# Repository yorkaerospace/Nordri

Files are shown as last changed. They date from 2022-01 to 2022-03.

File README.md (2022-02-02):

# Nordri

Nordri is a generic high-power rocket design.

## Features

- 54mm body, designed for postal tubes
- Fin assembly can be laser-cut from plywood
- Long 29mm inner tube for motor housing, designed to accommodate G and H motors up to 6 grains
- Mid-body break

## License

The designs in this repo are licensed under the [Creative Commons BY-SA 4.0 license](https://creativecommons.org/licenses/by-sa/4.0/).

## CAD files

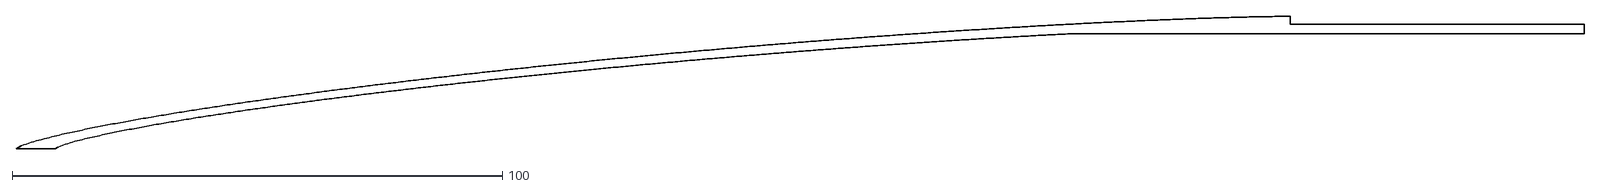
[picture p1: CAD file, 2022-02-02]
CAD/NoseSlice.dxf
320.0 x 27.0

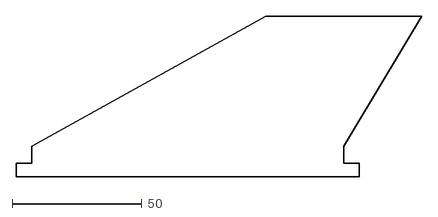
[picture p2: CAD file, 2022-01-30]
CAD/1Fin.dxf
156.0 x 61.6

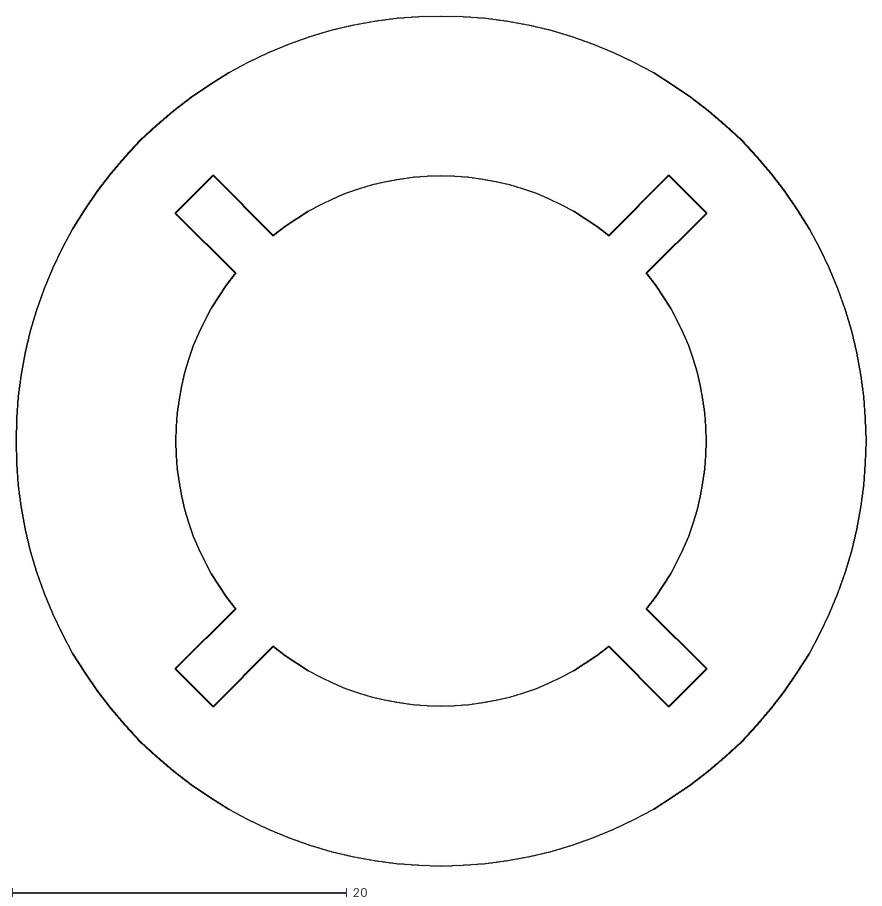
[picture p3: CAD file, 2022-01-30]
CAD/1Ring.dxf
50.8 x 50.8

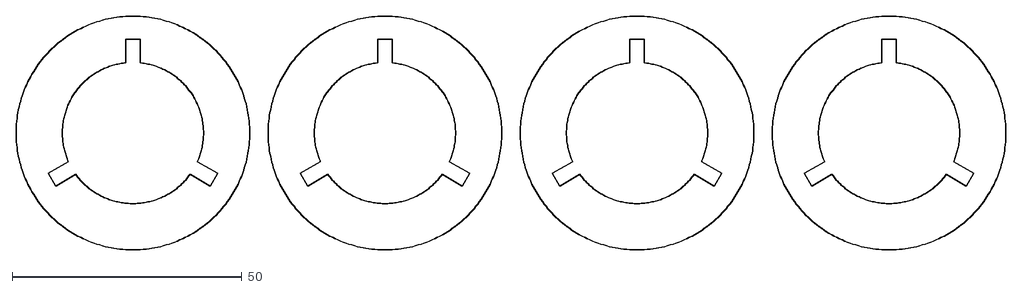
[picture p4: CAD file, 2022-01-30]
CAD/4Rings.dxf
215.2 x 50.8

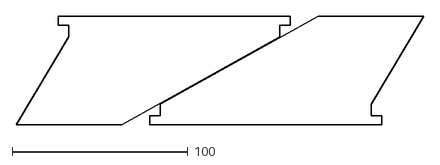
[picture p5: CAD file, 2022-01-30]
CAD/2Fins.dxf
232.0 x 61.7

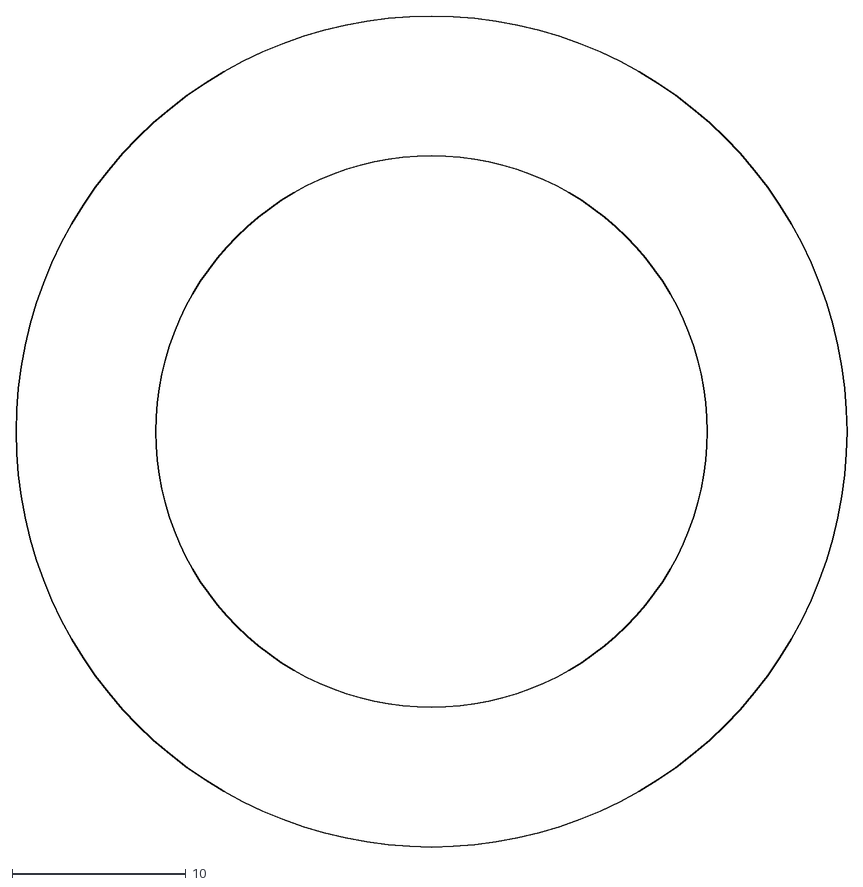
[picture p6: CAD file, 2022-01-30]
CAD/TopRing.dxf
47.8 x 47.8

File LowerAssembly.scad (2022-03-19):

// Laser Material Thickness
MATERIAL = 3.5;

// Tube dimensions
MAIN_OUTER = 54;
MAIN_INNER = 51;
COUPLER_INNER = 48.5;
TUBE_OUTER = 32;
TUBE_INNER = 29.5;
TUBE_LENGTH=200;

// Fin dimensions
FIN_THICKNESS = MATERIAL;
FIN_POINTS = [
    [0,0], [60,45], [100,45], [120,0]
];
FIN_ROOT = FIN_POINTS[len(FIN_POINTS)-1][0];
SLOT_HEIGHT = 5; // radial height of fin tabs

// Other
RING_THICKNESS = MATERIAL;
NUM_FINS = 4;
CORD_HOLE = 4; // diameter of the hole for the paracord
$fn = 100;

// Creates a 3d single fin on the xy plane aligned to 0,0
module Fin(){
    tab_len = (MAIN_OUTER - TUBE_OUTER)/2;
    linear_extrude(FIN_THICKNESS, center=true){
        union(){
            // Fin itself
            translate([0,tab_len,0]){
                polygon(FIN_POINTS);
            }
            // Main tab
            square([FIN_ROOT, tab_len], center=false);
            // Centering Slot
            translate([-RING_THICKNESS*2,-0.1,0]){
                square([FIN_ROOT + RING_THICKNESS*5, SLOT_HEIGHT+0.1], center=false);
            }
        }
    }
}

// Creates the n-fin assembly aligned around the inner tube
module Fins(){
    translate([0,0,FIN_ROOT+RING_THICKNESS*2])
    rotate([0,90,0]){
        for(i = [0 : 360/NUM_FINS : 360]){
            rotate([i, 0,0]){
                translate([0,TUBE_OUTER/2,0]){ Fin(); }
            }
        }
    }
}

// Model of the inner tube
module InnerTube(h=TUBE_LENGTH) {
    difference(){
        cylinder(h=h, d=TUBE_OUTER);
        cylinder(h=h, d=TUBE_INNER);
    }
}

module M3_nut(h=2.4, center=true) {
    // div by cos(30) converts hexagon side distance to corner distance

    LASER_TOLERANCE = 0.2;
    // Maximum width across flats (5.5)
    cylinder(h=h, d=5.5/cos(30)-LASER_TOLERANCE, $fn=6, center=center); 
    // Minimum width across flats (5.32)
    *cylinder(h=h, d=5.32/cos(30)-LASER_TOLERANCE, $fn=6, center=center); 
    // Minimum width across corners (6.01)
    *cylinder(h=h, d=6.01-LASER_TOLERANCE, $fn=6, center=center); 
}

module NutRetainer(w=10, h=3.5, nut=true){
    difference(){
        union(){
            color("red") 
            cube([w, MATERIAL*2 + h, MATERIAL], center=true);
            cube([w+8,h, MATERIAL], center=true);
        }
        if(nut) rotate(30) M3_nut(h=100);
    }
}

module Retainers(nut=false, h=3.5){
    rotate([0,90,0]){
        for(i = [360/NUM_FINS/2 : 360/NUM_FINS : 360]){
            rotate([i, 0,0]){
                translate([h/2,TUBE_OUTER/2 +4, 0]){ 
                    rotate([90,90,0]) NutRetainer(nut=nut, h=h);
                    }
            }
        }
    }
}

// Creates a ring on the xy plane with the fin slots cut out
module CouplerRing(){
    difference(){
        linear_extrude(RING_THICKNESS, center=false){
            difference(){
                circle(d=COUPLER_INNER);
                circle(d=TUBE_OUTER);
                translate([(TUBE_OUTER + CORD_HOLE) /2 -1,0,0]) circle(d=CORD_HOLE);
            }
        }
        Retainers(h=MATERIAL);
    }
}

module UpperFinRing(){
    difference(){
        linear_extrude(RING_THICKNESS, center=false){
            difference(){
                circle(d=MAIN_INNER);
                circle(d=TUBE_OUTER);
            }
        }
        Fins();
    }
}

module LowerFinRingTop(){
    difference(){
        linear_extrude(RING_THICKNESS, center=false){
            difference(){
                circle(d=MAIN_INNER);
                circle(d=TUBE_OUTER);
            }
        }
        Fins();
        for (r = [45: 180: 360]){
            rotate([0,0,r])
            translate([20,0,0])
            rotate([0,0,30]) M3_nut(h=10);
        }
    }
}

module LowerFinRingBottom(){
    difference(){
        linear_extrude(RING_THICKNESS, center=false){
            difference(){
                circle(d=MAIN_INNER);
                circle(d=TUBE_OUTER);
            }
        }
        Fins();
        for (r = [45: 180: 360]){
            rotate([0,0,r])
            translate([21,0,0])
            rotate([0,0,30]) cylinder(10,3, center=true);
        }
    }
}

// ---=== Render a pretty model ===---
module full_model(){
    InnerTube();
    // Fins in red
    color("red"){
        Fins();
    }
    translate([0,0,TUBE_LENGTH-RING_THICKNESS]) CouplerRing();
    translate([0,0,TUBE_LENGTH-RING_THICKNESS]) Retainers(nut=true);
    translate([0,0,TUBE_LENGTH-RING_THICKNESS*3]) CouplerRing();
    
    translate([0,0,FIN_ROOT + RING_THICKNESS*3]) UpperFinRing();
    translate([0,0,FIN_ROOT + RING_THICKNESS*2]) UpperFinRing();
    
    translate([0,0,RING_THICKNESS]) LowerFinRingBottom();
    translate([0,0,]) LowerFinRingTop();
    translate([0,0,-RING_THICKNESS]) LowerFinRingBottom();
}

full_model();

// Parts to cut
*projection() CouplerRing(); // x2
*projection() UpperFinRing(); // x2
*projection() LowerFinRingTop(); // x1
*projection() LowerFinRingBottom(); // x2
*projection() rotate([0,0,90]) Fin(); // x4
!projection() for(i = [0:6]) {
    translate([0, 11*i, 0]) NutRetainer();
}

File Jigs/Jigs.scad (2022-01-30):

include <./jigs_generic/rocket_base_clamp.scad>;
include <./jigs_generic/rocket_fin_clamp.scad>;

tube_diameter = 54;

fin_length = 50;
fin_thickness = 4;
num_fins = 4;

rocket_base_clamp(tube_diameter, fin_thickness);
translate([tube_diameter + fin_length * 2, 0, 0])
    rocket_fin_clamp(tube_diameter, fin_thickness, fin_length);

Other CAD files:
Jigs/JigsConcrete.scad
jigs/nordri_jogs.scad

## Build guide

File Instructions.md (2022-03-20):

# Instructions

## Lower Assembly

### Parts List

- Tubes
  - Outer Postal Tube (54mm x 185mm)
  - Inner Motor Tube (29mm x 200mm)
  - Coupler Tube (51mm x 110mm)
- Rings
  - Coupler Rings x2
    - Nut retainers x4
  - Upper Fin Rigs x2
  - Lower Nut Ring x1
  - Lower Fin Rings x2
  - Thrust Ring x1
- Fins x4
- Rail Button x1
- M3 Nut x6
- M3 Bolt 12 x6
- Thrust Ring x1
- 15 mm Screw x1
- Paracord ~25cm

### Steps

1. Laser cut rings and fins
1. Cut tubes to size
1. Create out thrust ring
1. Chamfer leading and trailing edges of fins
1. Sand glue surfaces on rings and tubes
1. Assemble couplers
1. Test fit fin rings & fins on inner tube
1. Cut fin slots into outer tube
1. Cut and tie paracord to size
1. Test fit with coupler & outer tube
1. Glue adjacent rings together
1. Tack lower rings with superglue
1. Attach fins and top fin rings with wood glue
1. Wait for inner assembly to dry
1. Drill retainer holes through thrust ring
1. Insert lower assembly into outer tube
1. Mask off fins, outer tube and paracord
1. Fillet coupler ring to inner tube and coupler
1. Fillet fins onto outer tube
1. Epoxy thrust ring to bottom of assembly (align with bolts)
1. Wait to partially dry (~2 hours)
1. Remove masking tape and twist bolts
1. Screw rail button into lower centering rings
1. Drill holes in main tube to attach to coupler
1. Paint

## Main Tube

### Parts List

- Postal Tube (54mm x 450mm)
- Rail button x1
- M3 16mm Bolt
- M3 Nut x1
- M3 Washers x1

## Steps

1. Drill hole as low as possible in the tube
1. Paint
1. Bolt rail button to the tube using nuts, bolts and washers
1. Fit check

## Nose Cone

### Parts List

- Nose Cone (3D printed?)
- Masking Tape

### Steps

- Create your nose cone (ours are 3D printed)
- Adding masking tape to shoulder
- Fit check with main tube

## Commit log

2021-11-16 Initial Nordri design
    [LowerAssembly.scad]
2022-01-26 Add CAD, Sudri prototype, new motor configs
    [1 Ring.dxf, 1Fin.dxf, 2 Fins.dxf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]
2022-01-26 Correct coupler mass
2022-01-28 Add Nose Cone, update cad
    [1 Ring.dxf, TopRing.dxf]
2022-01-28 Export nose cone slice to be revolved
    [NoseSlice.dxf]
2022-01-29 Adjust lower tube to put centering ring at top of coupler
2022-01-30 Add mid-fin clamp
    [jigs.scad]
2022-01-30 Rename to specifically be nordri
    [nordri_jogs.scad]
2022-01-30 COrrect filename typo
    [nordri_jigs.scad]
2022-01-31 Rename files to fit double-hump camelcase scheme
    [Jigs.scad]
2022-01-31 Rename to indicate concrete jigs, update generic jigs repo, update concrete jigs to match
    [JigsConcrete.scad]
2022-01-31 Correct masses and lengths in design, add motor configs
    [LowerAssembly.scad]
2022-01-31 Remove spaces from filenames
    [1Ring.dxf, 2Fins.dxf, 4Rings.dxf]
2022-02-02 Ensure correct nosecone dimensions
    [NoseSlice.dxf]
2022-02-07 Nordri rev.2
    Change fin profile
    Move rail buttons
    Label simulations
    Add ballast for M22
2022-02-07 Correct motor names with actual delays
2022-03-19 Shorten lower assembly to 200mm
2022-03-19 Add instrctions; update cad; modify lower assembly in design
    [LowerAssembly.scad]
